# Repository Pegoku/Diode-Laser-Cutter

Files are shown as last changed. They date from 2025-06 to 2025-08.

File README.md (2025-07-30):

# Diode-Laser-Cutter

This project is a 450 nm, 10 W diode laser cutter and engraver controlled by a BTT Rodent board running the FluidNC firmware.

## Why I made it?

I made this project as I wanted to learn how to design a small laser CNC to cut and engrave plywood. I also wanted to learn how to use the FluidNC firmware, as in the future I'd like to design a desktop CNC router, and I wanted to use the same firmware and board for it.

## Features

- Laser PWM control
- 10W diode laser
- 24V PSU
- Web interface for controlling the laser

## Images

Final Build
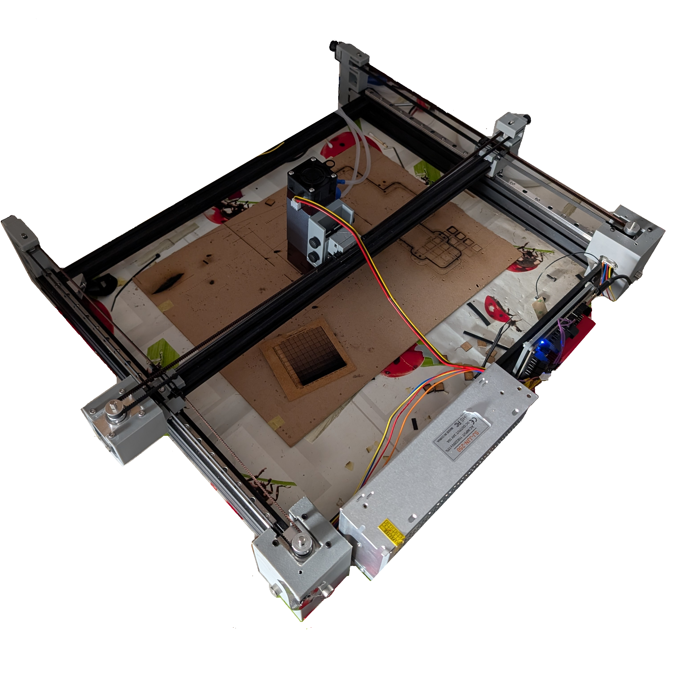
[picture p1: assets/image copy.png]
Final Build


Example of engraving
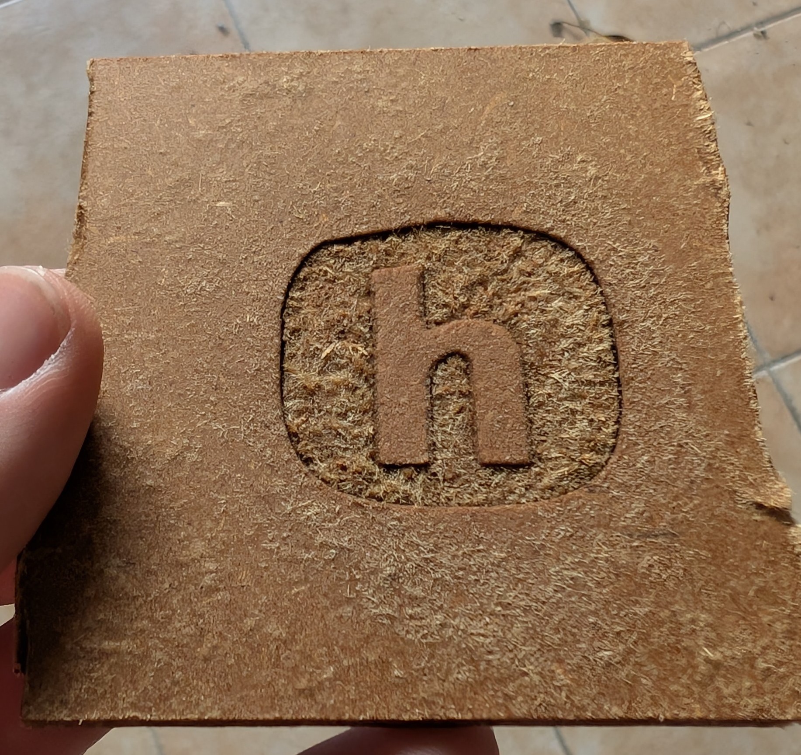
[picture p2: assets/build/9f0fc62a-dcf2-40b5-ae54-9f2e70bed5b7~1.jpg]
Example of engraving


<details>
  <summary>Final design</summary>

Final Design

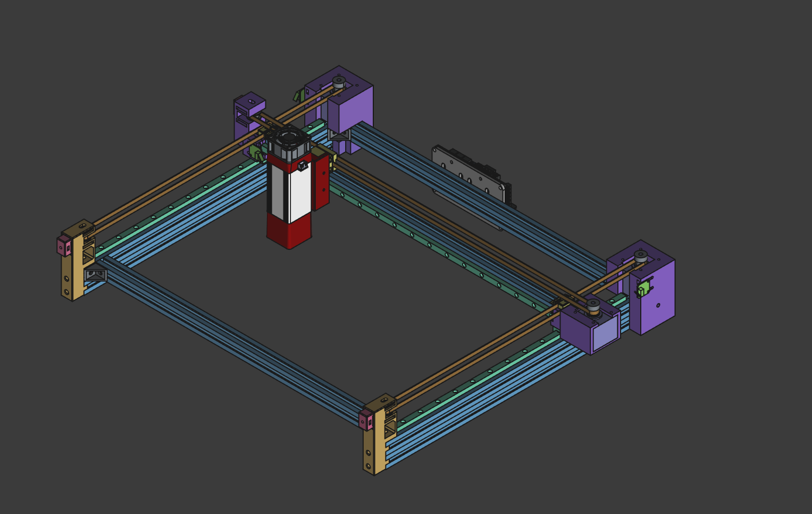
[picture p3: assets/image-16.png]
Final


</details>

<details>
  <summary>Pinout</summary>

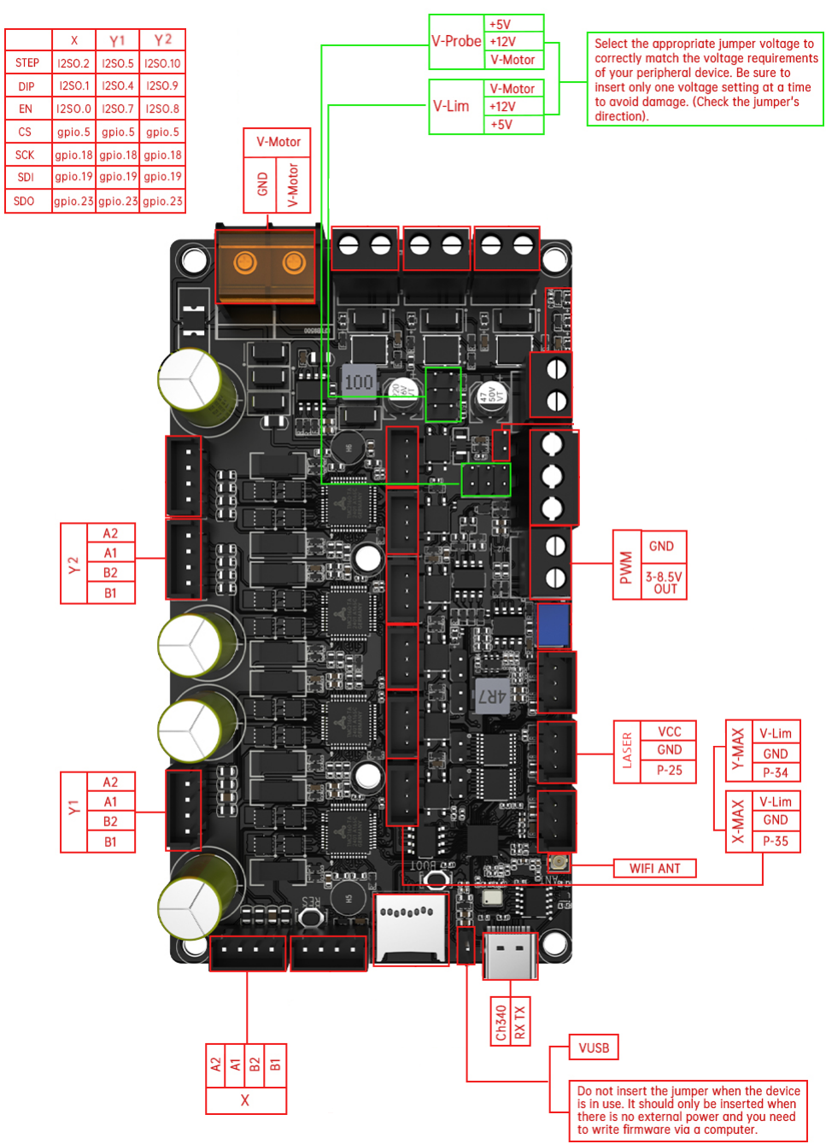
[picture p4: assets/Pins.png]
Pinout


</details>

## BOM

| Index | Part Number | What the item is for in your project | Pack Quantity | Qtty | Link | Unit Price | Total Price | Total (incl. VAT. shipping ...) | Total (incl. VAT. shipping ...) USD |
| ----- | --- | --- | --- | --- | --- | --- | --- | --- | --- |
| 1 | GT2 belt | Belt | 5m | 1 | https://www.aliexpress.com/item/1005001622058547.html | 6.09 € | 6.09 € | 300.06 € | $345.07 |
| 2 | M5x30mm pins | Belt tensioner idlers | 7 | 1 | https://www.aliexpress.com/item/1005007023343232.html | 2.25 € | 2.25 € | 4.29 € | $4.93 |
| 3 | ISO7380 M5x35mm | Screw | 10 | 1 | https://www.aliexpress.com/item/32810852732.html | 2.63 € | 2.63 € | |
| 4 | ISO7380 M5x20mm | Screw | 10 | 1 | https://www.aliexpress.com/item/32810852732.html | 1.59 € | 1.59 € | |
| 5 | ISO7380 M5x8mm | Screw | 10 | 1 | https://www.aliexpress.com/item/32810852732.html | 0.99 € | 0.99 € | |
| 6 | DIN912 M3x10mm | Screw | 50 | 1 [^*] | https://www.aliexpress.com/item/32810872544.html | 1.91 € | 0.00 € | |
| 7 | 2020 Corler bracket | Support for frame | 10 | 1 | https://www.aliexpress.com/item/1005008208638104.html | 2.44 € | 2.44 € | |
| 8 | Nema 17 stepper motor | Motor | 1 | 3 | https://www.aliexpress.com/item/1005005281739306.html | 6.59 € | 19.77 € | |
| 9 | BTT Rodent | Controller | 1 | 1 | https://www.aliexpress.com/item/1005008016124632.html | 51.34 € | 51.34 € | |
| 10 | 2020Tx500 | Aluminum extrusion | 1 | 1 | https://www.aliexpress.com/item/1005005893301224.html | 7.59 € | 7.59 € | |
| 11 | 2020Tx550 | Aluminum extrusion | 1 | 2 | https://www.aliexpress.com/item/1005005893301224.html | 8.19 € | 16.38 € | |
| 12 | T-nut M5 | T-Nut for aluminum extrusion | 50 | 1 [^*] | https://www.aliexpress.com/item/1005004157015035.html | 2.30 € | 0.00 € | |
| 13 | MGN9Cx400 | Linear Rail | 1 | 2 | https://www.aliexpress.com/item/4000264234020.html | 12.29 € | 24.58 € | |
| 14 | MGN9Cx500 | Linear Rail | 1 | 1 | https://www.aliexpress.com/item/4000264234020.html | 13.99 € | 13.99 € | |
| 15 | 2040Tx450 | Aluminum extrusion | 2 | 1 | https://www.aliexpress.com/item/1005003300082630.html | 15.69 € | 15.69 € | |
| 16 | Laser LT-80W 24V | Laser | 1 | 1 | https://www.aliexpress.com/item/1005003306807390.html | 121.94 € | 121.94 € | |
| 17 | Air pump A | Air pump option A | 1 | 1 | https://es.aliexpress.com/item/1005008823630481.html  | 6.59 € | 6.59 € | |
| 18 | Air pump B | Air Pump option B | 1 | 1 | https://es.aliexpress.com/item/1005007667077158.html  | 10.19 € | 10.19 € | |
| 19 | 24V/10A PSU | PSU | 1 | 1 | https://es.aliexpress.com/item/33051556213.html | 22.79 € | 22.79 € | |
| 20 | Limit Switches | Homing | 5 | 1 | https://es.aliexpress.com/item/1005007124540078.html  | 3.49 € | 3.49 € | |
| 21 | Discount code | Discount code | 1 | 1 | ATOLLSES40 | -40.00 € | -40.00 € | |
| 22 | Hand Screw | Belt tensioning | 10 | 1 | https://es.aliexpress.com/item/1005007775607843.html  | 2.59 € | 2.59 € | |
| 23 | Idler | Belt Idler | 1 | 3 | https://es.aliexpress.com/item/32817328238.html | 1.20 € | 3.60 € | |
| 24 | Pulley | Belt Pulley | 1 | 3 | https://es.aliexpress.com/item/32781681772.html | 1.18 € | 3.54 € | |

[^*]: Parts already owned, not included in the total price

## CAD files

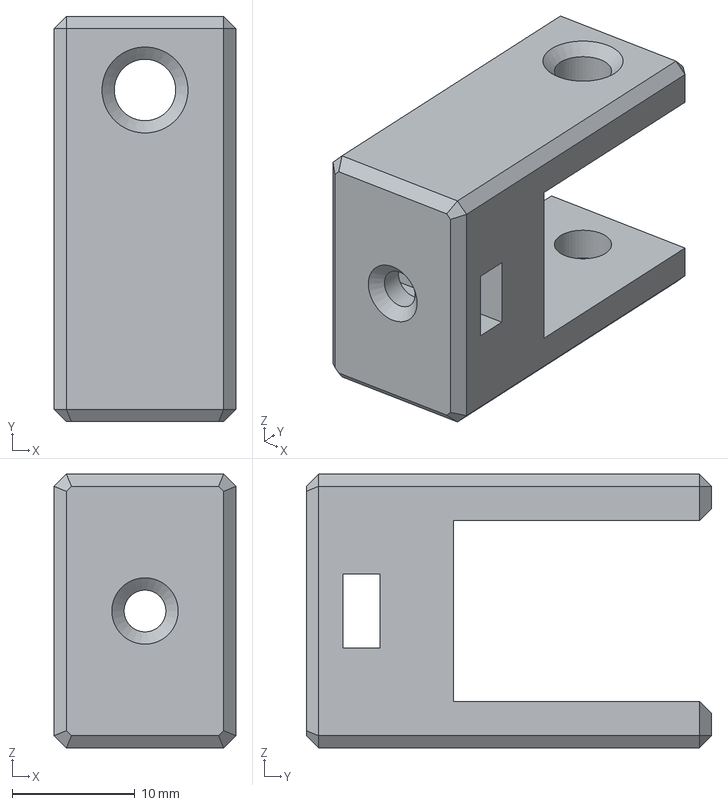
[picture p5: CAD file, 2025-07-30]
CAD/LaserCutter-X GantryBelt Tensioning3.step
14.8 x 33.0 x 22.3 mm

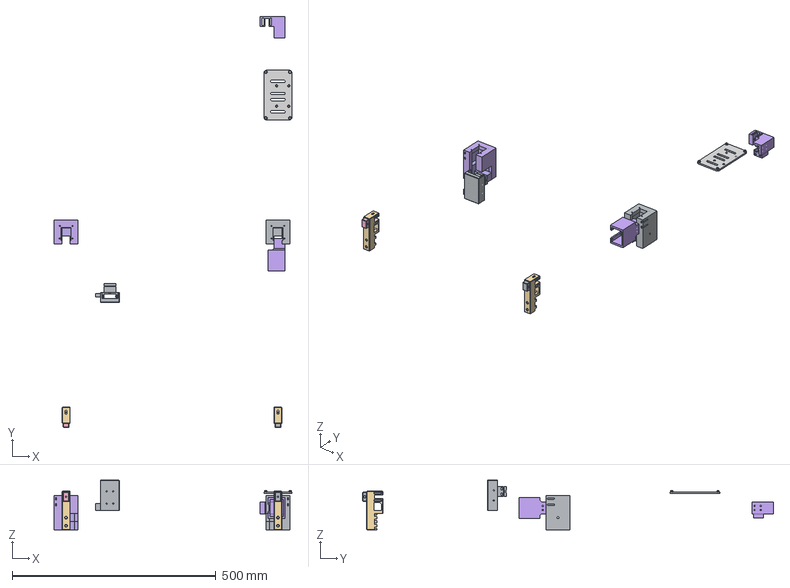
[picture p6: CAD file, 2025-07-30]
CAD/printedParts.step
583.8 x 1009.0 x 122.0 mm
Idler Support2
Belt Tensioning2
MotorHolderX2
MotorHolderX1
MotorHolderA
MotorHolderB
Belt Tensioning1
Scale002
Scale001
Idler Support

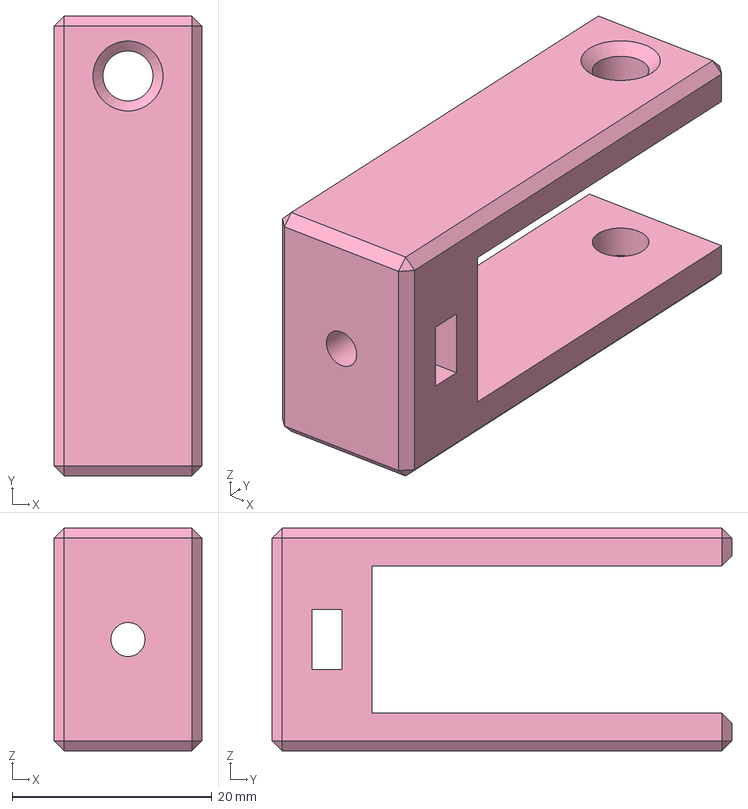
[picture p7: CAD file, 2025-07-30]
CAD/printedParts3.step
14.8 x 46.0 x 22.3 mm

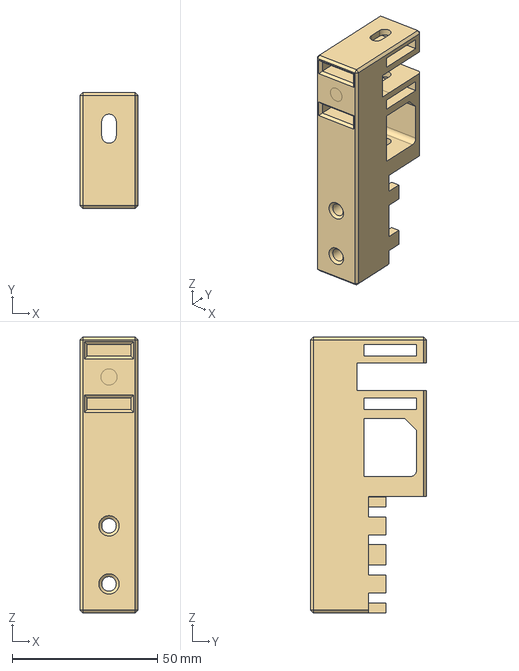
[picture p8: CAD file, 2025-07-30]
CAD/LaserCutter-Y Support 1Idler Support.step
20.0 x 40.0 x 95.0 mm

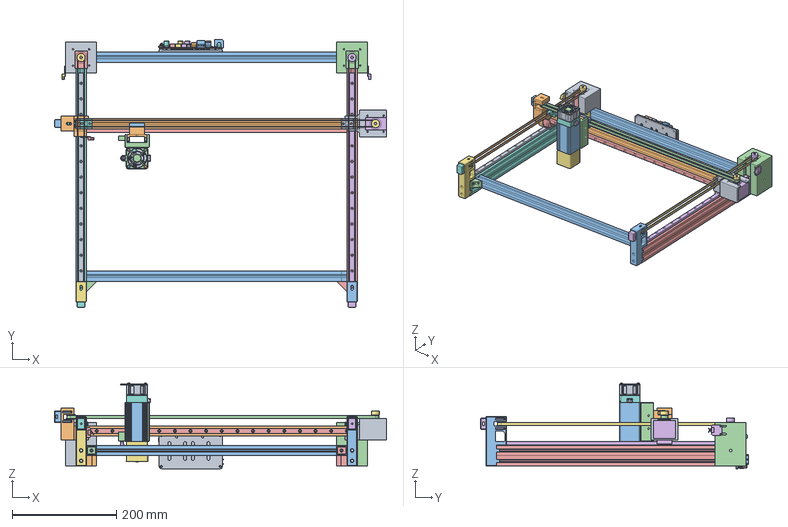
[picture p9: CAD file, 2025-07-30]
CAD/LaserCutter.FCStd
637.1 x 513.7 x 164.5 mm
DO-214AC-S1G-1.xtd
C1206 (2).xtd
C1206 (2).xtd001
C0805.xtd
C0805.xtd001
C0805.xtd002
C0805.xtd003
C0805.xtd004
C0805.xtd005
C0805.xtd006
C0805.xtd007
C0805.xtd008
C0805.xtd009
C0805.xtd010
C0805.xtd011
C0805.xtd012
C0805.xtd013
C0805.xtd014
C0805.xtd015
DFN8_3x3.xtd
DFN8_3x3.xtd001
DFN8_3x3.xtd002
DFN8_3x3.xtd003
DFN8_3x3.xtd004
DFN8_3x3.xtd005
DFN8_3x3.xtd006
DFN8_3x3.xtd007
DFN8_3x3.xtd008
DFN8_3x3.xtd009
DFN8_3x3.xtd010
DFN8_3x3.xtd011
DFN8_3x3.xtd012
DFN8_3x3.xtd013
DFN8_3x3.xtd014
DFN8_3x3.xtd015
PEC0510.xtd
PEC0510.xtd001
PEC0510.xtd002
PEC0510.xtd003
KEY-SMD_4P-L42-W32-P220-LS.xtd
KEY-SMD_4P-L42-W32-P220-LS.xtd001
KF128_3P.xtd
254_1x2PIN_DIP.xtd
XH2_54-4P_step.xtd
XH2_54-4P_step.xtd001
XH2_54-4P_step.xtd002
XH2_54-4P_step.xtd003
TSSOP-16-1.xtd
254_1x2PIN_DIP.xtd001
5.08_2Pjiexian.xtd
res_2512.xtd
XH-A-3.xtd
XH-A-3.xtd001
XH-A-3.xtd002
SL-D.xtd
3362S-1-103.xtd
5.08_2Pjiexian.xtd001
C3225-1.xtd
DO-214AC-S1G-1.xtd001
DO-214AC-S1G-1.xtd002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

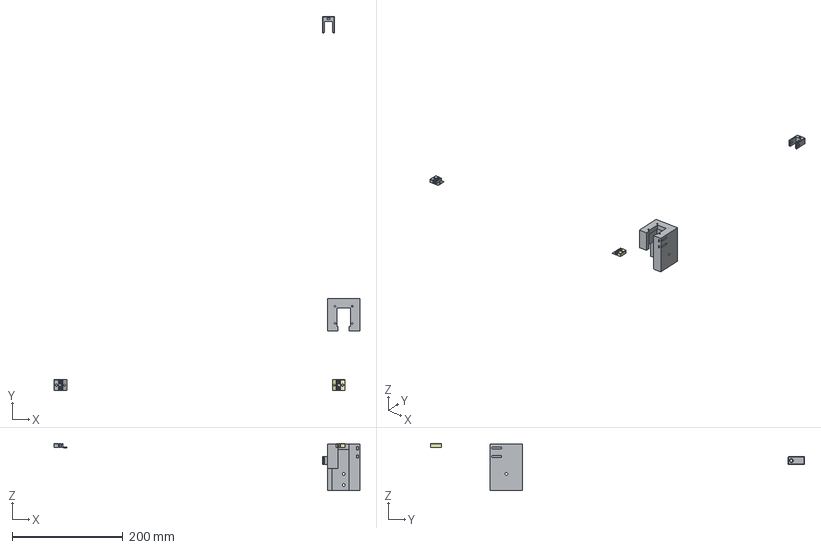
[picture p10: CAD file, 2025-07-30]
CAD/printedParts2.step
552.0 x 675.3 x 85.0 mm
MotorHolderA
Belt Tensioning3

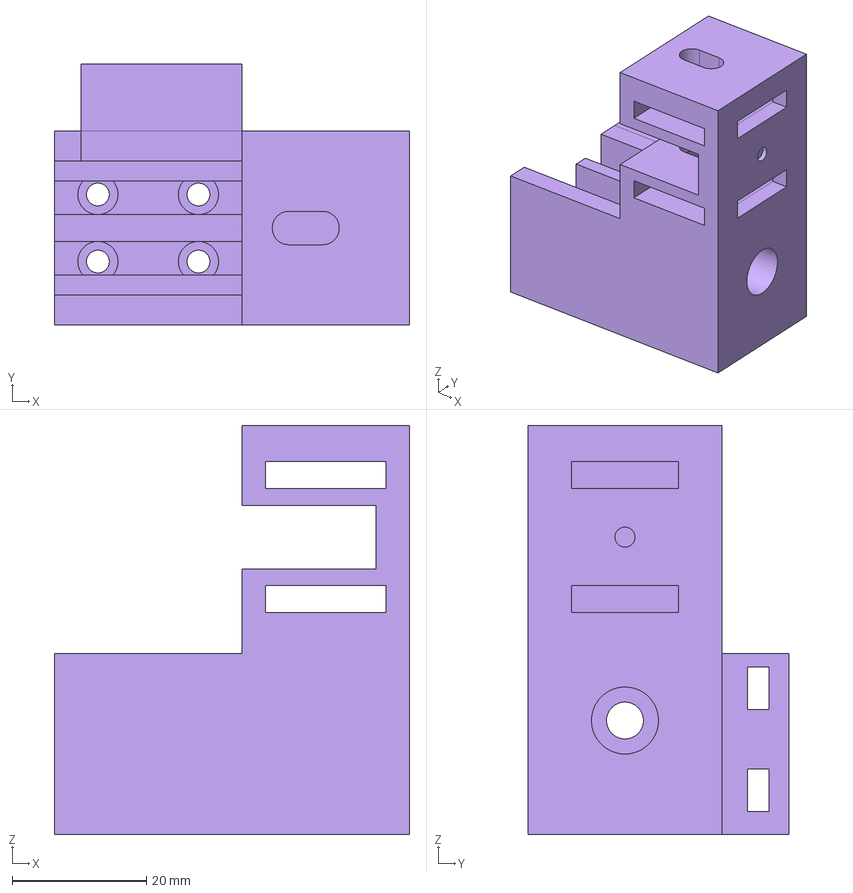
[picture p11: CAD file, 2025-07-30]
CAD/printedParts4.step
53.0 x 38.9 x 61.0 mm

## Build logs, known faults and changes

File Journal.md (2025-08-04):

|---
title: "Diode Laser Cutter"
author: "Pegoku"
description: "CNC Laser Cutter/engraver with a diode laser"
created_at: "2025-06-18"
total_time_spent: "83h"
---

# June 18th: Mockup and first components
First day of the project. I wanted to get an idea of what (and how) I'd like to build the laser cutter. That's why I did a few sketches to which I then selected the best one.
Sadly this was made during class, so I don't have any pictures of the sketches. :sob:

But I can tell you that it had a simple structure, with the dimensions of 400x500mm and a square laser head. It would use linear rails for all the axes and a ball screw on each axis to be able to move rigidly and accurately.

I would also use a CNC controller and probably one with an esp32 as I wanted to use the [FluidNC](http://wiki.fluidnc.com/en/home) firmware (a really cool firmware for esp32-based CNC controllers) as I had never used it and I love esp32.

I started looking for some components, the one of which I started with was the controller, as it would limit the components I could use. After quite a bit of research I found the [BTT Rodent](assets/https://biqu.equipment/products/bigtreetech-rodent). A full featured controller, It is a bit overkill for my project, but I wanted to try it out, as in the future I would like to do a CNC router and could use it for that too, so I'd already be experienced with it.

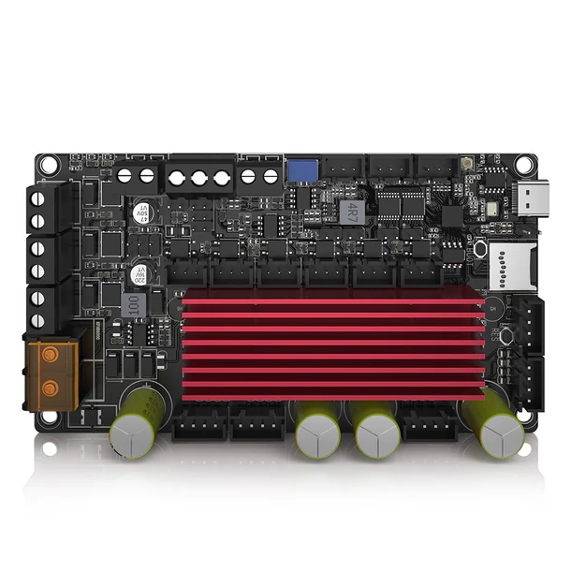
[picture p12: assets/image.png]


Once I arrived home, as I already had the controller, I searched for a laser, and after quite a bit of searching, I went with a Diode Laser, as it was the most affordable option and it could cut wood and acrylic, which is what I wanted to cut. I found this [laser](https://es.aliexpress.com/item/1005003306807390.html) on aliexpres, it was quite pricey (for the budget I have), but it's the best one I could find with that specs. It has a 10W output, which is enough to cut 5mm wood and acrylic, and it has a square head, which will be helpful for the mounting bracket.

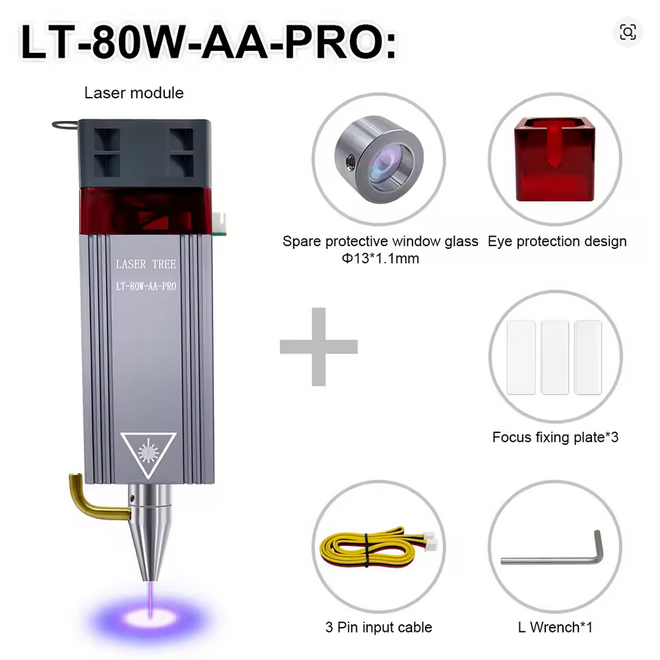
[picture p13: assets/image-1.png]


After that, I started looking for the structure I wanted to do. I planned in the sketches I'd use 2020 aluminum extrusions, so I started looking for them. I first checked aliexpress, but they were quite expensive, so I searched for other suppliers, and found JLCMC, a subsidiary of JLCPCB, which is a PCB manufacturer. They had a really good price for the extrusions, so I started using them for the structural materials. 
I ended up with:
- 1x 2020x540mm extrusion, as I wanted to have 20mm of space on each side - X axis.
- 2x 2040x440mm extrusions, as I wanted to have 20mm of space on each side too, and 2040 would help the the machine be more rigid and taller. - 2x Y axis.

Then, I started looking for the linear rails, and did quite a bit of research, but it was getting late, so I decided to leave it for the next day.

PS: sorry for not having images of the sketches

**Total time spent: 8h**

# June 19th: More components and starting the design
Today was the first day of summer holidays, so I had all day to work on the project.
First, I continued looking for the linear rails. I didn't know which ones to choose, as I have never used them before, so I had to do research (the best part of all projects). As I was looking for them in JLCMC, there were quite a few options, but I ended up with the BMW9C-1-L500-Z1-C-E20 linear rails. They weren't too expensive, and had the characteristics I wanted, so I went with them. I got 1x 500mm rail for the X axis, and 2x 400mm rails for the Y axis.

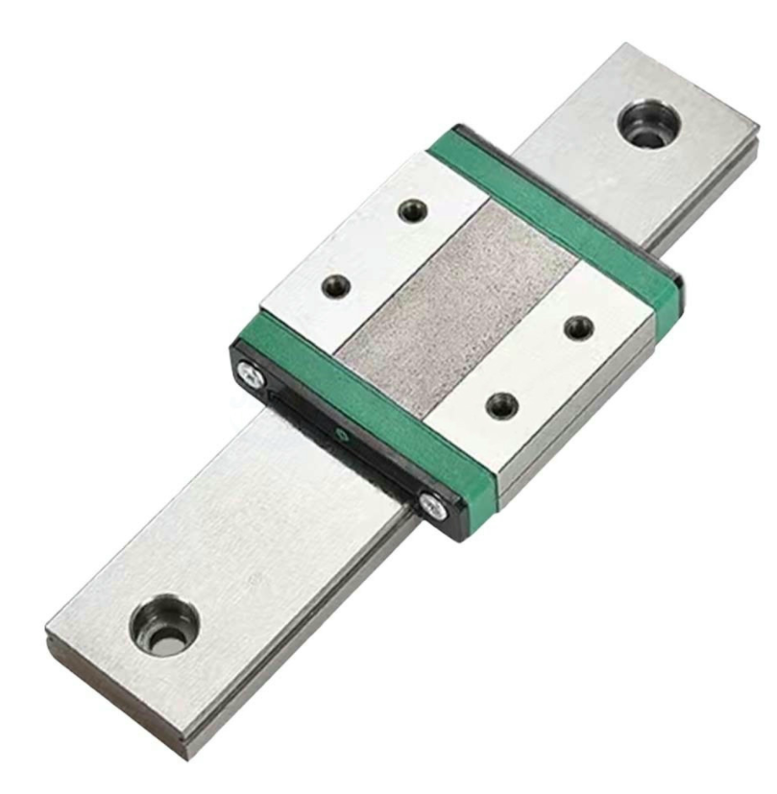
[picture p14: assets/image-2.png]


And now the last component I needed (for the base structure) was the ball screws. I thought they would be cheap (that's why I wanted to use them), but they were quite more expensive than I expected. So I thought for quite long, other ways I could use to move the axes, and ended up using GT2 belts. They are not as rigid as the ball screws, but they are way cheaper and easier to find.

After having the basic parts, I started designing the base of the frame in FreeCAD.
I started creating a template for the 2020 extrusions so I could easily create new ones of any size.

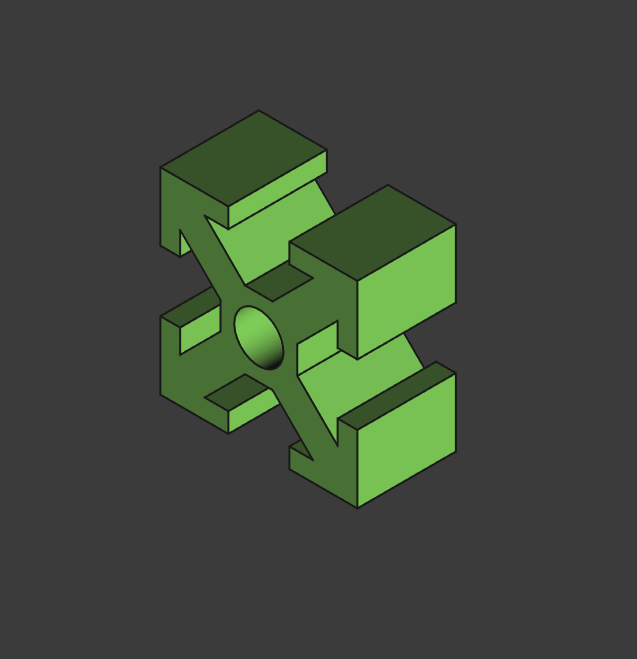
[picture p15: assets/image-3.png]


I did the same for the linear rails. I also searched for a 3d model of the Rodent controller, which was quite hard, but I finally found it.

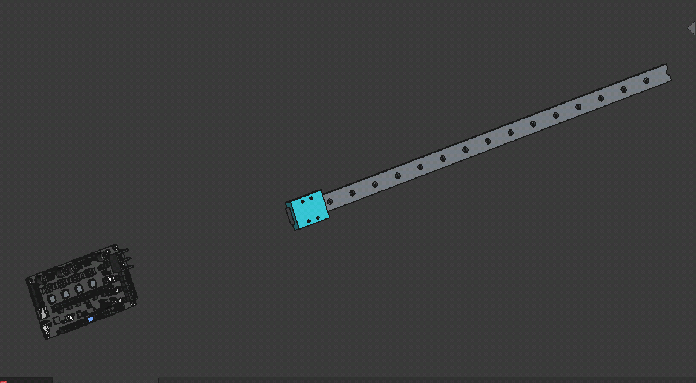
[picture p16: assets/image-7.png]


After that, I started creating the base frame. First, I did the X axis, which was quite easy, as it was just a 2020 extrusion with a linear rail.

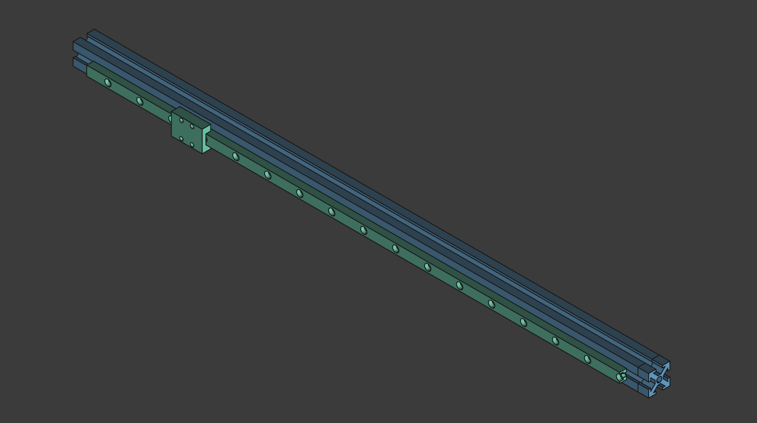
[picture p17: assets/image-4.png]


Then I did the Y axis. I had to do 2x as I wanted to have 2 Y axes, one on each side of the X axis. I used 2040 extrusions for the Y axis, as I wanted it to be more rigid and taller. I also added the linear rails to the Y axis.

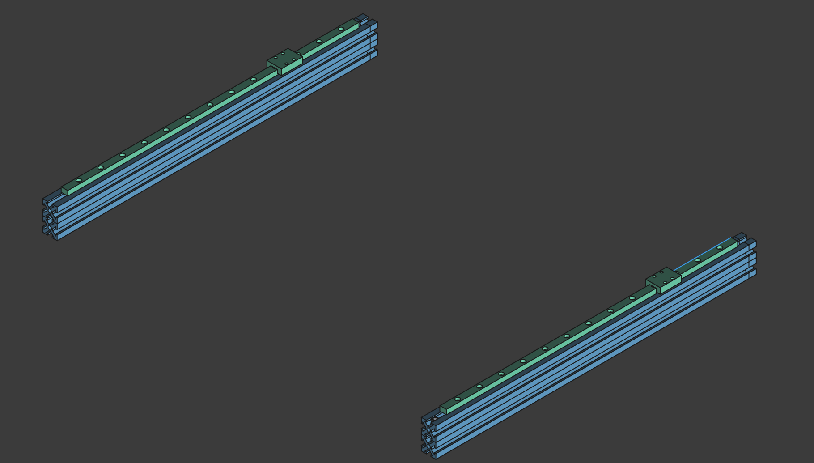
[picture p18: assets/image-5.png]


After that, I combined everything to create the base frame. I also added a rear 2020 extrusion to hold the Y axes together.

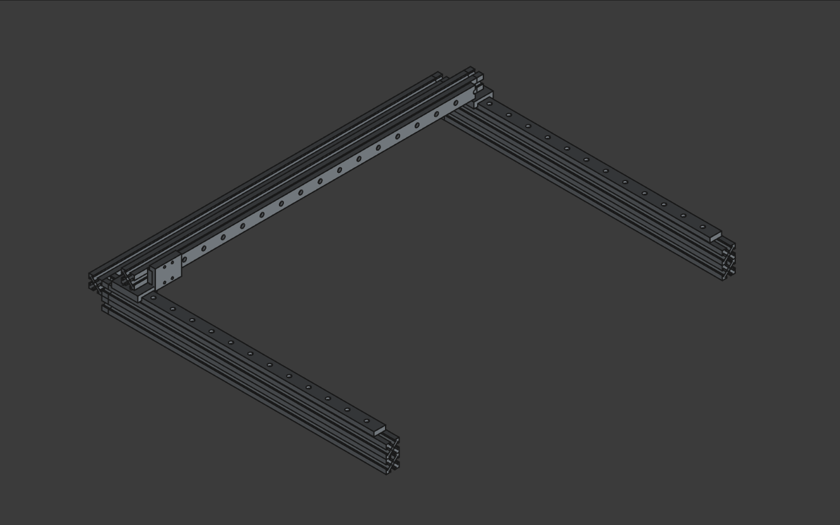
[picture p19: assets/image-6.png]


## Motors and pulleys
Now I had to find the motors I would use. I didn't know which ones to use, nor how many or where to put them, so I did some research and found that NEMA 17 motors would be the best option for this lightweight machine. What I wan't sure was about the Y motor, I wanted to use 2x motors, one on each side of the Y axis, but it seemed a bit too much, also the controller only has 1 Y stepper output. But when I realised how easier it would be to have 2x motors, I decided to use one of the remaining stepper drivers (Z) for the second motor.

Then, I searched how would the belts be mounted, but ended up leaving it for the future me, as I didn't know how to do it currently. What I did was to add the [motors](https://es.aliexpress.com/item/1005005281739306.html), [pulleys](https://es.aliexpress.com/item/32781681772.html) and [idlers](https://es.aliexpress.com/item/32817328238.html) to the model. 

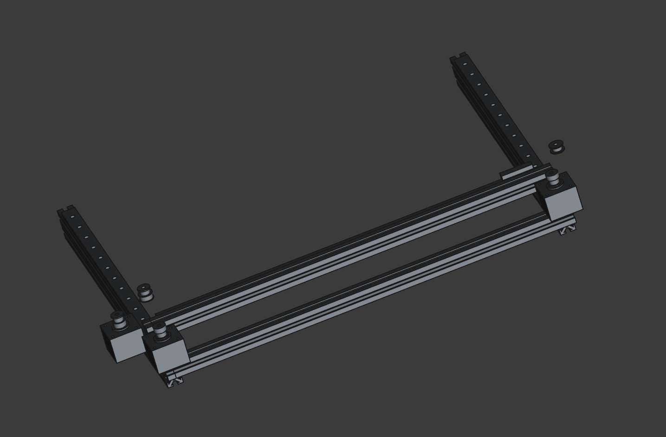
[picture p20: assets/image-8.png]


Now was time for one of the hardest parts of the project (imo, for now). The belt tensioners. I have never used nor designed them, so I had to search online what they are, how they work and maybe some example. Luckily I found a tutorial on how to tension GT2 belts on a voron 2.4, which helped me to understand how they work and how I could design one. I ended up with a a quite simple design, which I think will work. It consists of a 3d printed support for the idler, with a C-shaped piece and a 30mm M5 pin for the idler to be mounted on. The C-shaped piece has a hole with a M3 nut where a M3 screw will be used to tension the belt. I'm not sure if it will work, nor if I explained it well, but I will show you the model so you can see how it works.

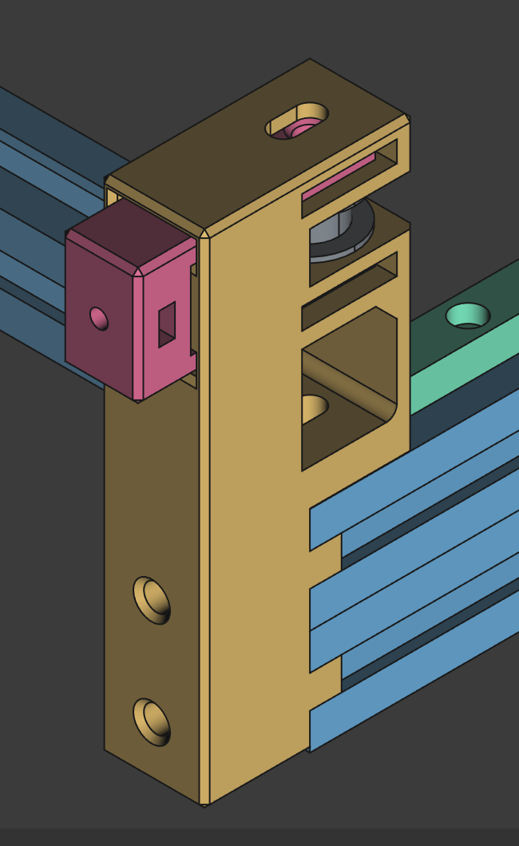
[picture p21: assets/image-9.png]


To continue, I had to find a way to mount the motors to the frame. I started with the Y motors as they seemed the easiest ones. I designed a simple bracket that would hold the motor to the 2020 extrusion. I'm not sure if it's the best way to do it, but it seems to work.

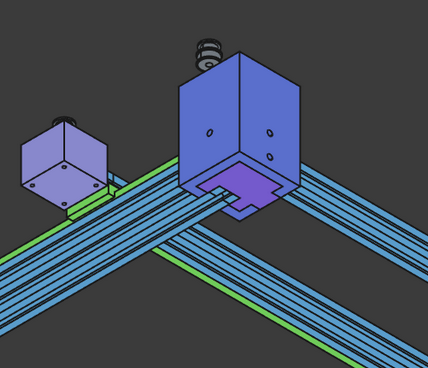
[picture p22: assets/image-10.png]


**Total time spent: 13h**

# June 20th: Continuing with the design and JLC SHIPPING!

## JLC shipping!
While designing, I checked the JLC shipping price. But what happened was unexpected, the shipping price was over 120$! This was a no-go, as I didn't have that much budget for the project, so I had to search for other supplier and ended up with the original aliexpress ones. They were a bit more expensive, specially the aluminum extrusions, but the shipping was free (and faster), so it was a way better option. The aluminum extrusions were the same, but the linear rails were a diferent model, they were MGN9C instead of BMW9C. Hope they work.

## Motors and Belts
Now I had all the tensioning components for the belts for Y axis. This is how it looks like:

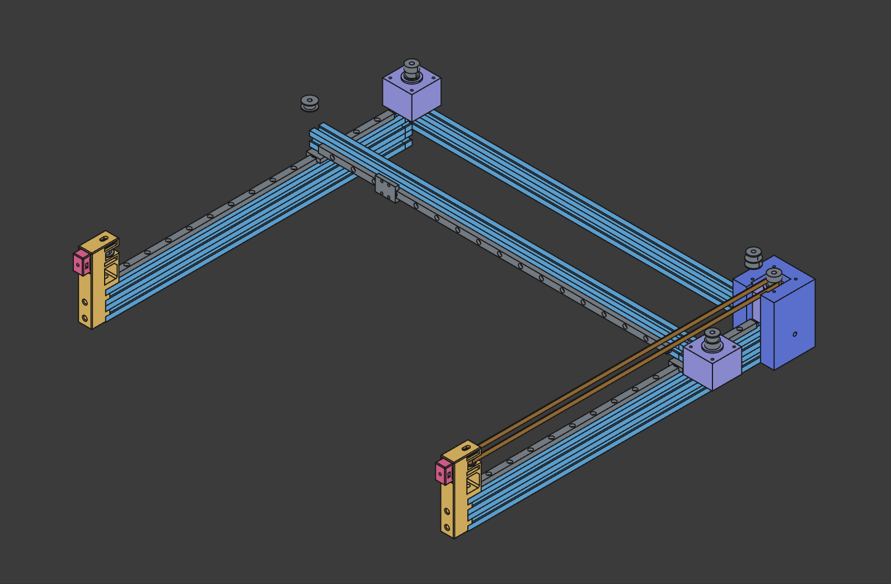
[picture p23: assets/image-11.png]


I also designed the X axis motor mount, which worked as the mount for the rail too.

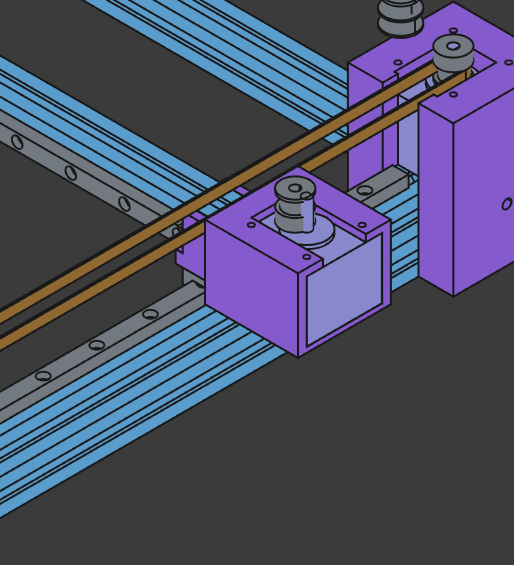
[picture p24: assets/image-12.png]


Once I had the motor mount, I started designing the X axis belt tensioner. It was quite similar to the Y axis one, but the main piece had a diferent shape, as it had to be mounted on the 2020 extrusion and it had to be used as a support for the linear rail.

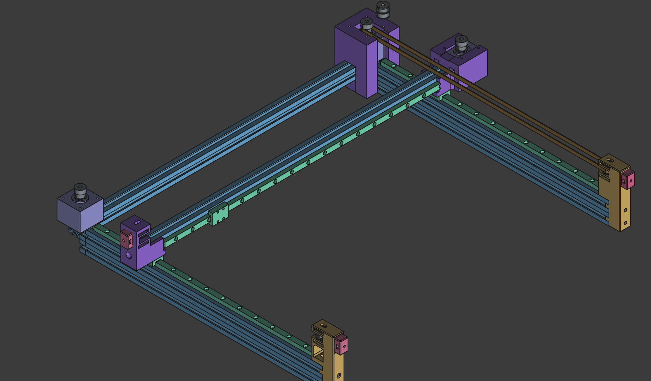
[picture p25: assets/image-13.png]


After that, I added the 2nd motor holder which was the same as the first one, but mirrored. I also added a 2020 extrusion to the front of the frame to hold the Y axis together. And to secure it I added 2020 brackets to the extrusions.
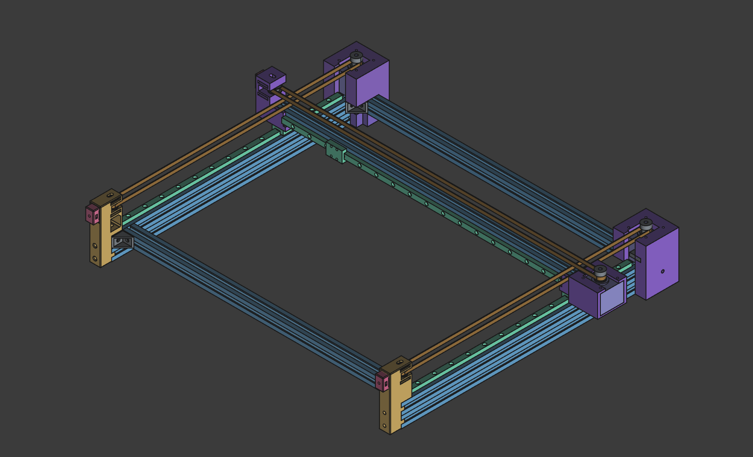
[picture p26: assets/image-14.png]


**Total time spent: 9h**

# June 21th: Aliexpress shopping
Today I didn't want to design much, so I just focused on searching for the components and trying to get the best deals I could find.

I spend all day searching for the components, and ended up with quite a good list. It was overbudget, but luckily, I got a 40€ discount coupon, so I could buy everything I needed, and still have some budget left. Sadly the coupon ends in 4 days, so I hope i get accepted before that.

[BOM](BOM.csv)

**Total time spent: 8h**

# June 22th: Laser head and coding
Today was the last day. I had to design the laser head, which was the last part of the machine.
I used the original laser head, and created a mount for it. Luckily, I found a 3d model of the laser head, so I just had to create a mount for it. I designed it to be mounted on the X axis rail, and to be able to move up and down, so I could focus the laser.

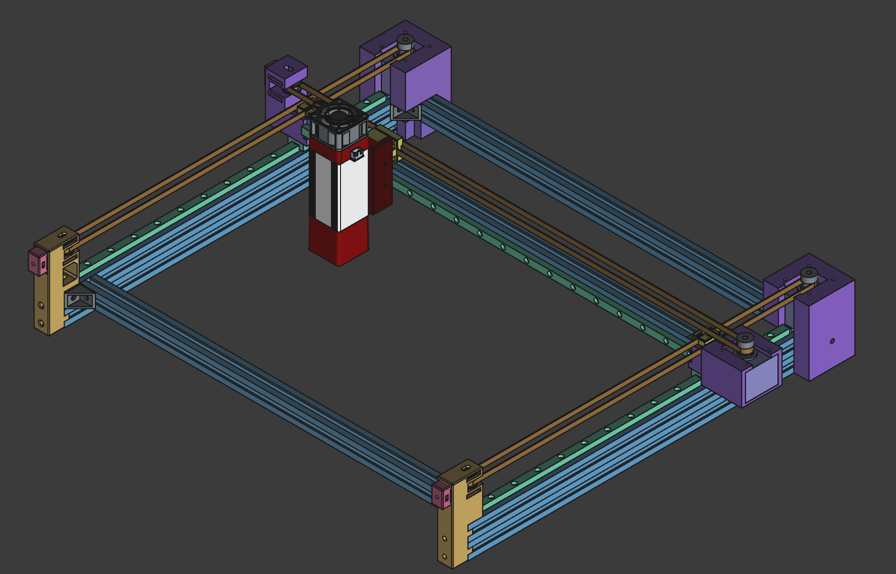
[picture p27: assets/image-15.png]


As a last thing, I added endstops to the machine, and the controller mount. The endstops were quite easy, once I found a good endstop, and the controller was quite easy too.

Final design:



Now I only had to code the machine. I used FluidNC, and luckily, there was a template for the Rodent controller, so I just had to copy it and change a bit the configuration. eg. adding dual Y motors, enabling PWM, etc.

**Total time spent: 7h**

# July 22th: Start the build
After quite a long wait. All (almost) the pieces have arived!!
Today I started the build. First, I built the frame to see how big it would be, and to see if I had the minimum pieces to build it. I did it, but the floor was a bit uneven, so I put some wood under the legs to make it flatter. 
Then I realized I had to cut the 2020 extrusions, as they were too long, so I cut them to about the right size using a hacksaw.

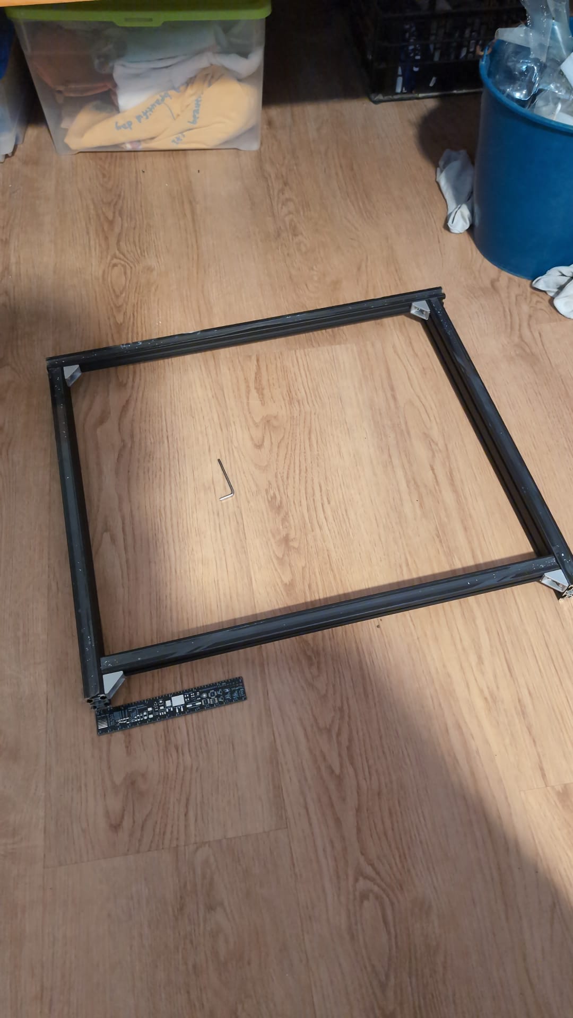
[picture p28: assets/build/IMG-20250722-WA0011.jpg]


After that, I grabbed all the printed parts I had, and started removing the supports. That took quite a while, as I had used auto-generated supports, which were quite hard to remove. But I finally got them all removed.

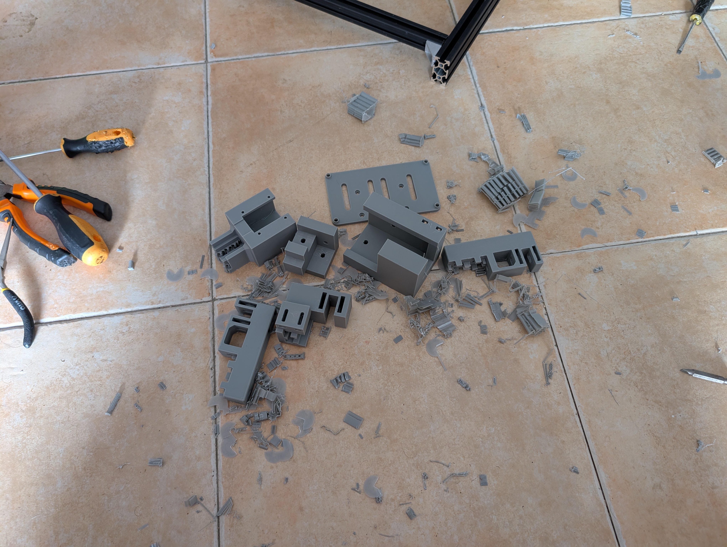
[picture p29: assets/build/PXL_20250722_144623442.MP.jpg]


To continue, I placed the motor in the printed case, and I had to modify it a bit, as I hadn't thought about the motor connector, so I had to cut a bit of the case to make it fit. After that, I placed the motor in the case and it fit snugly.

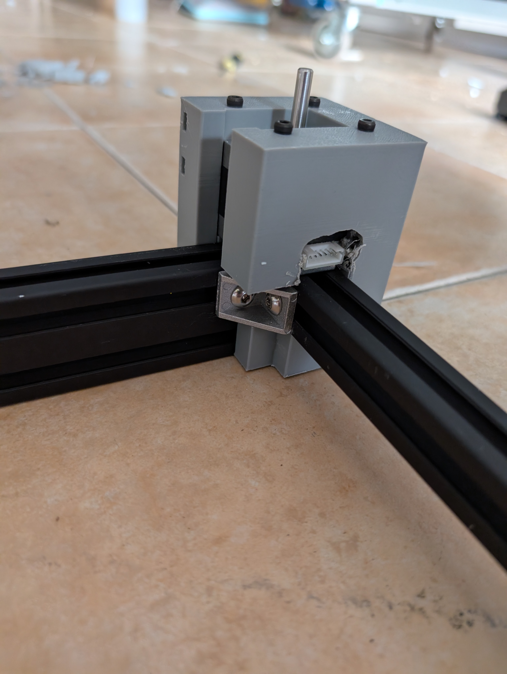
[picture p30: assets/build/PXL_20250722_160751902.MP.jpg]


Then I placed both Y idler supports, which fit snugly too. 

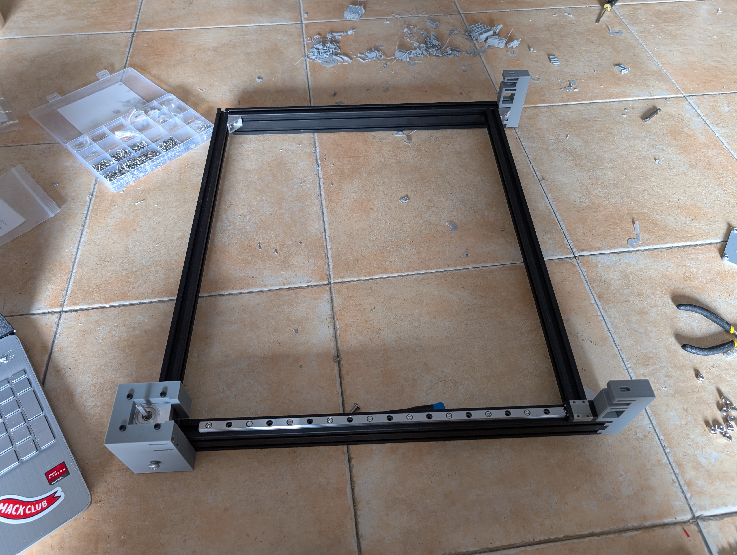
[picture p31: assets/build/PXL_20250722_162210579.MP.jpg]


After that, I screwed both Y linear rails to the extrusions. I also added the idlers to the supports, which they weren't correctly designed, as the idlers couldn't be tensioned.

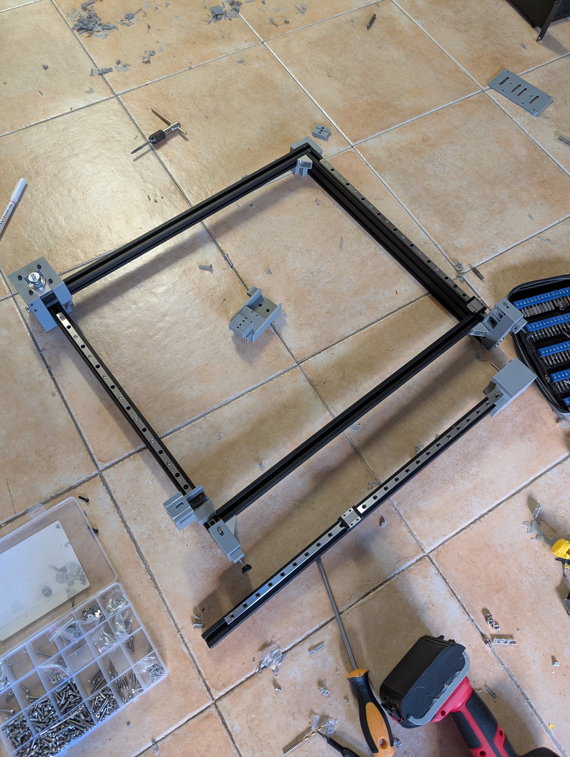
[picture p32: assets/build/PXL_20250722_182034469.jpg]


To fix: motor holders and idler supports.

**Total time spent: 6h**

# July 23th: Continuing the build
Today I continued the build. All the fixed and remaining prints finished printing.
First, I placed the 2nd motor, which I already had printed, so I had to modify it too.

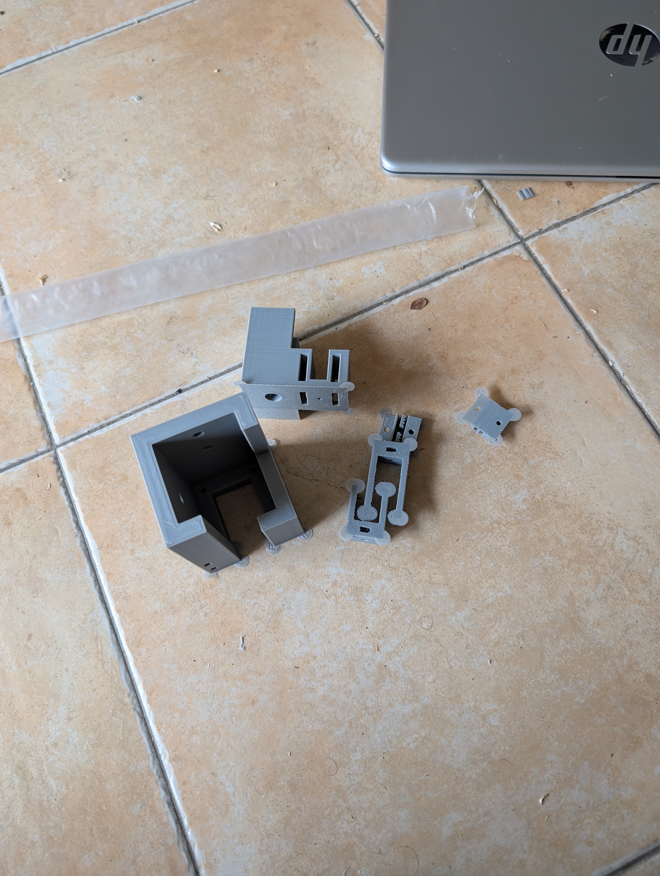
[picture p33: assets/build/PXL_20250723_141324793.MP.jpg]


Then, I screwed the X linear rail to the X axis extrusion, and aligned it with the printed pieces. 

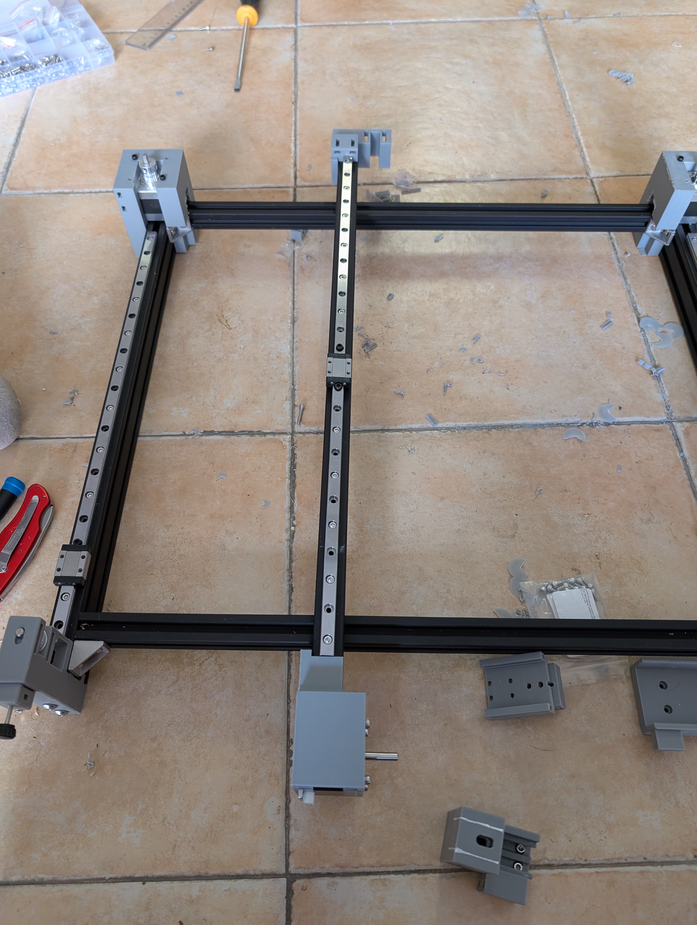
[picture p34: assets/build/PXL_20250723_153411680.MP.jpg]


Afterwards, I realised that the X axis would be hard to place, as the extrusion was on top of the screw holes. So I had to remove the printed parts from the X extrusion, remove the linear blocks from the rails and screw them to the printed parts. I used a holder-thingy to hold the balls from the linear blocks, so they wouldn't fall out. Then I slowly placed the linear blocks on the rails. This was a tense moment, as I didn't want to lose any balls, but luckily it worked and I could mount the X axis!

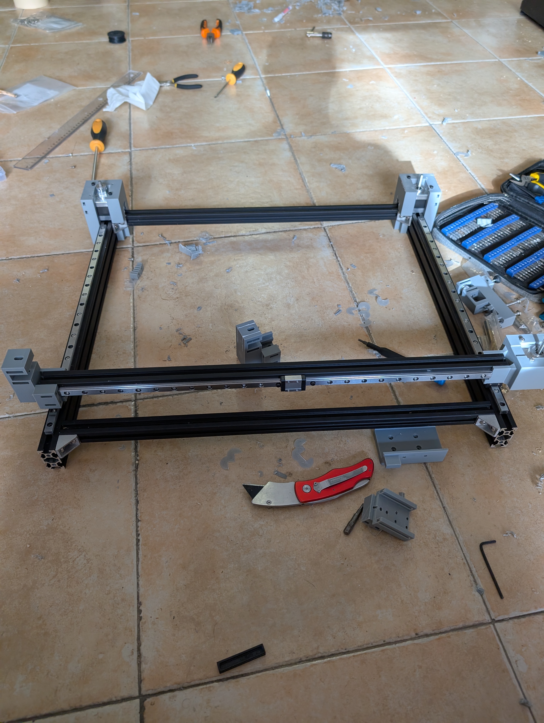
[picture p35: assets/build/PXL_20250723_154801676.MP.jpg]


To finish, I placed the new idler supports, which were designed to be able to fit the idlers and to be tensioned. I also placed the new X idler mount, which also had a design error.

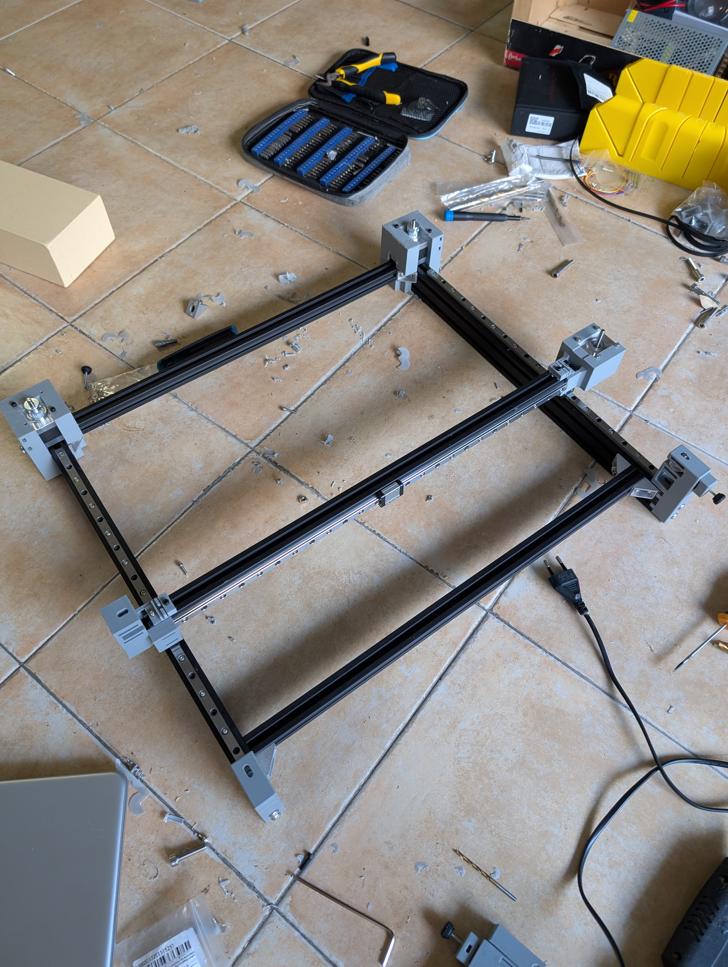
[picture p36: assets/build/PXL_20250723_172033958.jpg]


PS: I also noticed the screws I needed to use M6 screws for the extrusions, not M5, so I went and bought some M6 screws, as I didn't have any, and the next day I'll screw them to the extrusions.

**Total time spent: 5h**

# July 24th: Tapping is my passion 😭
First, I fixed the belt tensioners, as the nut was too loose and it spun freely, as I didn't use a square nut, so I just used hot glue to hold it in place. I also added a M2.5 washer to the M3 screw end, so it wouldn't damage the plastic when tightening it (it did before). 

Today I spent a LOT of time tapping the extrusions (I spent +3.5h tapping), but it was worth it. I had to tap all the extrusions, and drill some passthrough holes for some screws. I used a M6 tap, and also had to drill the printed parts to fit the M6 screws.

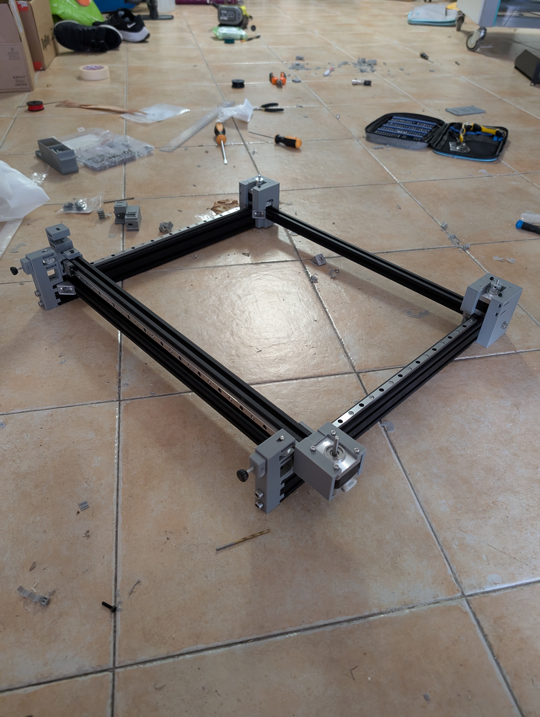
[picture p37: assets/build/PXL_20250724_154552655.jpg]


I made another mistake, one of the rear motor screw wasn't long enough, so I had to spin fast the screw so it melted the plastic and could screw to the extrusion. 

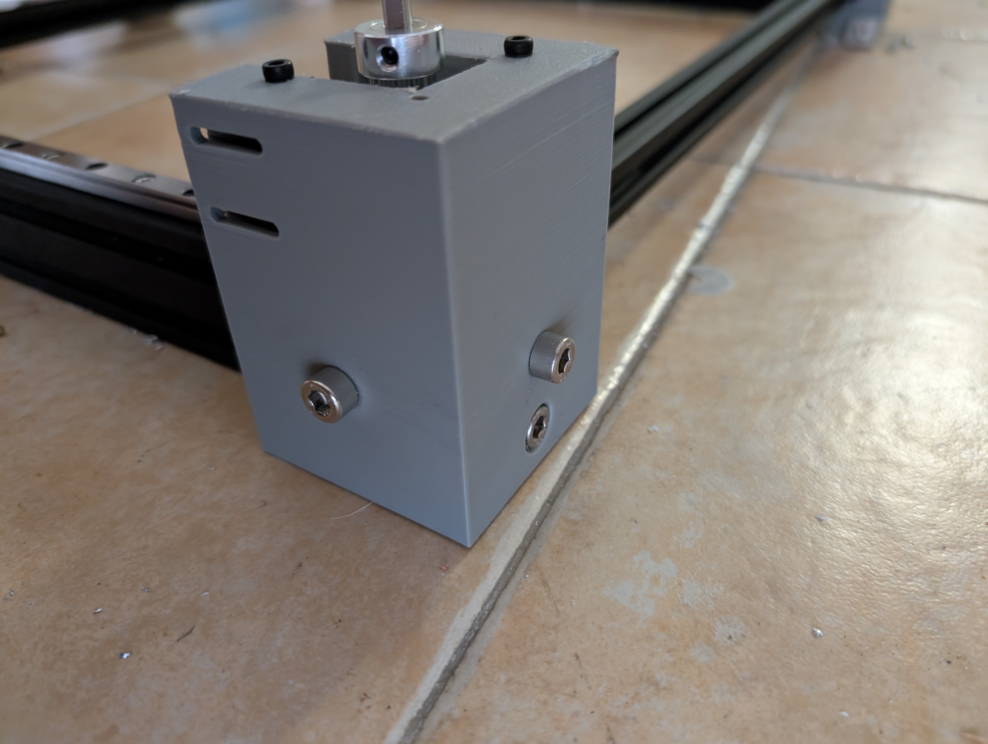
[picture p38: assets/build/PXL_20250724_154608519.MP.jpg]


But overall, I think it turned out quite well.

I also mounted the Laser on the X axis, which was quite easy, except for the fact that I had to drill new holes to the laser support, as I had designed it wrong. Was an easy fix, though.

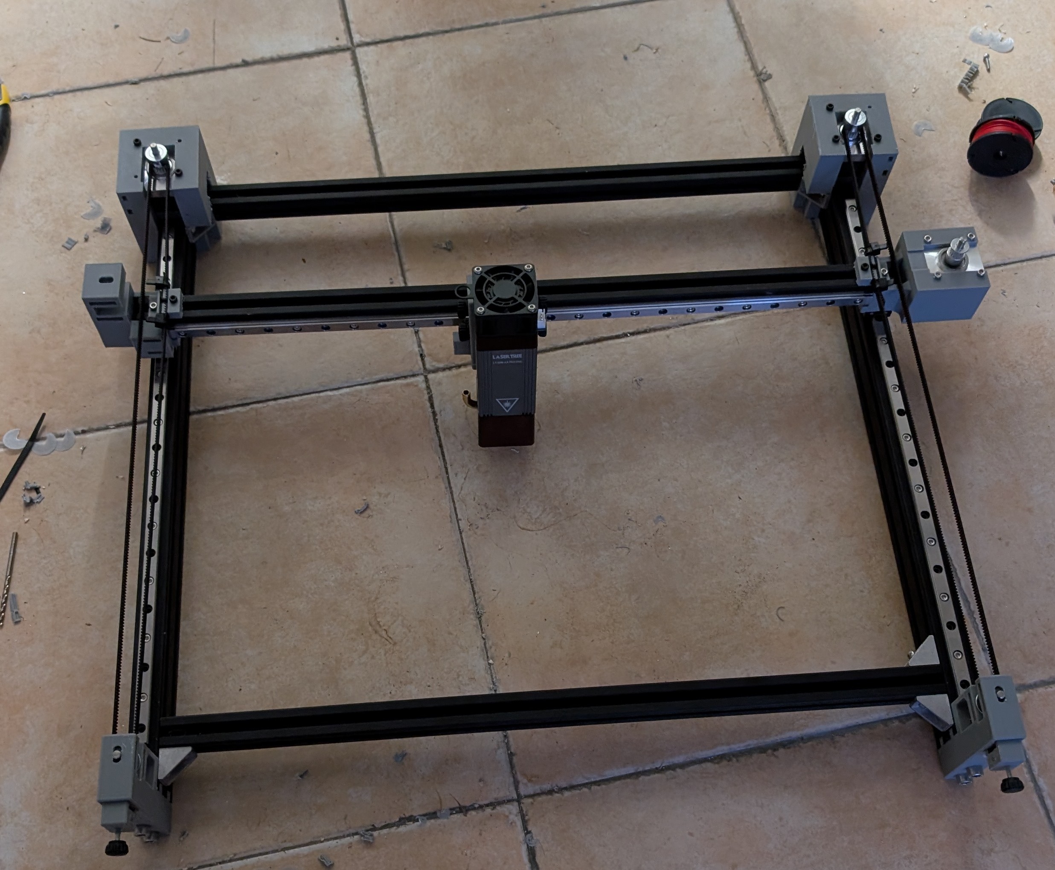
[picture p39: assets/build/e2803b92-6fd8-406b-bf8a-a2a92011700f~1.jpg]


Also, while I was at it, I wanted to connect the laser belt, but I realised I had only ordered 2 pulleys and idlers for the printer, and I needed another one, so I ordered them online, and to skip the wait, I tried getting them from an old printer I had, but sadly they were too small, so I just had to wait for them to arrive.

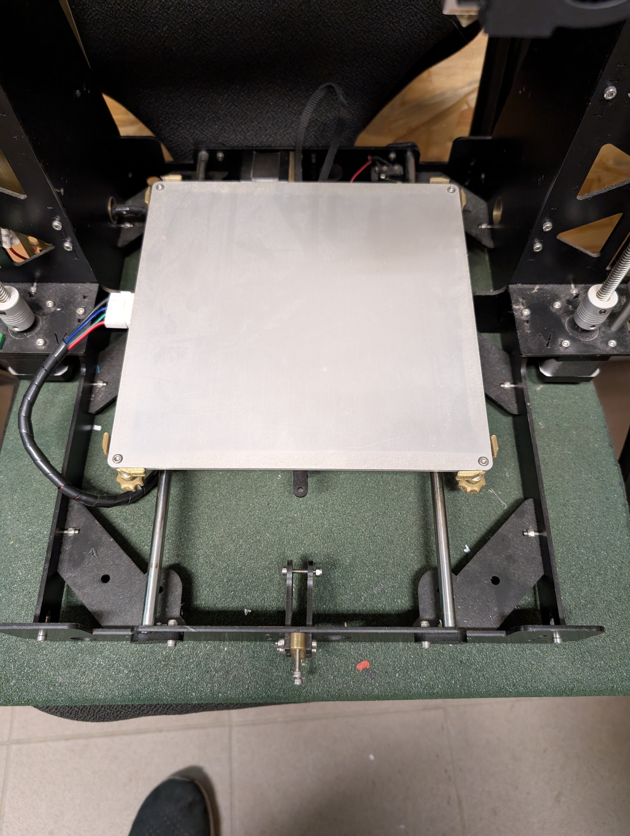
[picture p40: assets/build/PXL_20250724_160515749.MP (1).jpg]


**Total time spent: 7h**

# July 25th: Electronics and wiring
Today I mounted the electronics to the frame, and started wiring everything.
First, I mounted the controller (BTT Rodent) to the frame, which was quite easy, as I just had to screw it to the frame using T-nuts. I also mounted the power supply, which was a bit harder, as I wanted it to be mounted using t-nuts too, but there weren't any holes. So I just dissasembled the PSU and replaced drilled two nuts of the PSU and replaced the screws with longer ones so I could screw it to the frame.

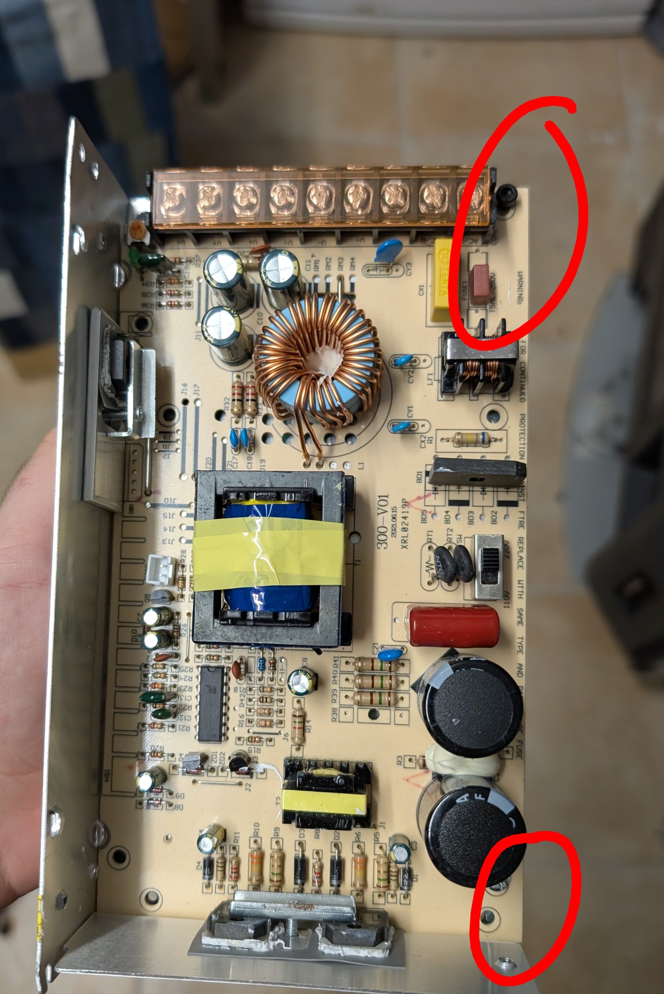
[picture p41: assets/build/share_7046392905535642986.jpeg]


I also wired the controller and power supply, I only needed to wire the laser, and motors.



**Total time spent: 5.5h**

# July 26th: Wiring the Y motors
Today I wired and configured both Y motors, which was quite easy. Sadly, I didn't have a crimper in hand, nor the right connector, so I just used pin receptacles soldered to the stepper wires. First, I thought I had configured something wrong, (maybe too little current), so I increased the current to 3A, twice the motor current, but it still didn't work, it just vibrated. Then I noticed I had connected a motor phase in reverse, so I just swapped the wires, and it worked! Then I played with them a bit, and also used the laser for the first time, which was quite fun. While doing that, I realised the motors were quite hot, and I didn't remember why. But while reviewing the config, I saw the 3A current 😅 , so I reduced it to the recommended 1.5A, and it worked perfectly.

<video controls src="assets/build/PXL_20250726_225948615~2.mp4" title="Title"></video>

**Total time spent: 3h**

# July 27th: Wiring the X motor and belt
Today the pulleys and idlers arrived! So I could wire the X motor and belt. I first mounted the idler, which was quite easy, except for a design flaw, which made the belt tensioner almost unusable. Then I mounted the pulley to the motor, which was quite easier, as I just had to use a M3 setscrew to hold it in place.
Then, I mounted the belt to the X axis, which was a quite hard to tension, but luckily I was able to do it using zipties.

After that, I crimped the wires to the motors, wired and configured them.
Then, I did some calibrations to the laser, like, the power and speed, speed and passes, accuracy, and my favourite, the shake test.









Shake test

While doing the tests, I fixed the config, and finally I did my first real ~~print~~ cut. It was for my robotics team, and it was a success!!, quite fast too. I did with cardboard, and then with wood.



**Total time spent: 7h**

# July 28th: Final configuration and 3d engraving!
Today I finished the configuration of the laser, and also wanted to test something I saw online. 3D engraving. To do it, I tested with the HackClub logo, which I had to convert to a grayscale image, and then to gcode using LaserGRBL. The result, after quite a few tries, was quite good.

First try:



Second try:



Second try after cleaning:



**Total time spent: 4.5h**

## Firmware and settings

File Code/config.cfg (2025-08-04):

board: BTT Rodent V1.0
name: BTT CNC
meta: (07.2025) by Pegoku
kinematics: {}
stepping:
  engine: I2S_STREAM
  idle_ms: 255
  pulse_us: 4
  dir_delay_us: 1
  disable_delay_us: 0
axes:
  shared_stepper_disable_pin: NO_PIN
  x:
    steps_per_mm: 40
    max_rate_mm_per_min: 10000
    acceleration_mm_per_sec2: 1000
    max_travel_mm: 300
    soft_limits: false
    homing:
      cycle: 1
      positive_direction: false
      mpos_mm: 150
      feed_mm_per_min: 200
      seek_mm_per_min: 200
      settle_ms: 500
      seek_scaler: 1.1
      feed_scaler: 1.1
    motor0:
      limit_neg_pin: NO_PIN
      limit_pos_pin: NO_PIN
      limit_all_pin: gpio.35:low
      hard_limits: false
      pulloff_mm: 1
      tmc_5160:
        step_pin: i2so.2
        direction_pin: i2so.1
        disable_pin: I2SO.0
        cs_pin: gpio.5
        spi_index: 1
        r_sense_ohms: 0.022
        run_amps: 1.5
        hold_amps: 0.5
        microsteps: 8
        toff_disable: 0
        toff_stealthchop: 5
        use_enable: false
        run_mode: CoolStep
        homing_mode: Stallguard
        stallguard: 3
        stallguard_debug: true
        toff_coolstep: 3
        tpfd: 4
  y:
    steps_per_mm: 40
    max_rate_mm_per_min: 10000
    acceleration_mm_per_sec2: 1000
    max_travel_mm: 300
    soft_limits: false
    homing:
      cycle: 1
      positive_direction: true
      mpos_mm: 150
      feed_mm_per_min: 100
      seek_mm_per_min: 200
      settle_ms: 500
      seek_scaler: 1.1
      feed_scaler: 1.1
    motor0:
      limit_neg_pin: NO_PIN
      limit_pos_pin: gpio.34
      limit_all_pin: NO_PIN
      hard_limits: false
      pulloff_mm: 1
      tmc_5160:
        step_pin: i2so.5
        direction_pin: i2so.4:low
        disable_pin: I2SO.7
        cs_pin: NO_PIN
        spi_index: 2
        r_sense_ohms: 0.075
        run_amps: 1.5
        hold_amps: 0.5
        microsteps: 8
        toff_disable: 0
        toff_stealthchop: 5
        use_enable: false
        run_mode: CoolStep
        homing_mode: CoolStep
        stallguard: 3
        stallguard_debug: false
        toff_coolstep: 3
        tpfd: 4
    motor1:
      limit_neg_pin: NO_PIN
      limit_pos_pin: gpio.33
      limit_all_pin: NO_PIN
      hard_limits: false
      pulloff_mm: 1
      tmc_5160:
        step_pin: i2so.10
        direction_pin: i2so.9:low
        disable_pin: I2SO.8
        cs_pin: NO_PIN
        spi_index: 3
        r_sense_ohms: 0.075
        run_amps: 1.5
        hold_amps: 0.5
        microsteps: 8
        toff_disable: 0
        toff_stealthchop: 5
        use_enable: false
        run_mode: CoolStep
        homing_mode: CoolStep
        stallguard: 3
        stallguard_debug: false
        toff_coolstep: 3
        tpfd: 4
  a:
    steps_per_mm: 157.75
    max_rate_mm_per_min: 18000
    acceleration_mm_per_sec2: 1500
    max_travel_mm: 325
    soft_limits: true
    homing:
      cycle: 1
      positive_direction: true
      mpos_mm: 150
      feed_mm_per_min: 100
      seek_mm_per_min: 800
      settle_ms: 500
      seek_scaler: 1.1
      feed_scaler: 1.1
    motor0:
      limit_neg_pin: NO_PIN
      limit_pos_pin: gpio.32:pu
      limit_all_pin: NO_PIN
      hard_limits: false
      pulloff_mm: 1
      tmc_5160:
        step_pin: i2so.13
        direction_pin: i2so.12
        disable_pin: I2SO.15
        cs_pin: NO_PIN
        spi_index: 4
        r_sense_ohms: 0.022
        run_amps: 0.5
        hold_amps: 0.5
        microsteps: 16
        toff_disable: 0
        toff_stealthchop: 5
        use_enable: false
        run_mode: CoolStep
        homing_mode: CoolStep
        stallguard: 16
        stallguard_debug: false
        toff_coolstep: 3
        tpfd: 4
i2so:
  bck_pin: gpio.22
  data_pin: gpio.21
  ws_pin: gpio.17
spi:
  miso_pin: gpio.19
  mosi_pin: gpio.23
  sck_pin: gpio.18
sdcard:
  cs_pin: gpio.0
  card_detect_pin: NO_PIN
  frequency_hz: 8000000
i2c0:
  sda_pin: gpio.27
  scl_pin: gpio.26
status_outputs:
  report_interval_ms: 500
  idle_pin: I2SO.11:low
  run_pin: I2SO.14:low
  alarm_pin: I2SO.3:low
Laser:
  output_pin: gpio.13:pd
  s0_with_disable: false
  disable_with_s0: false
  speed_map: 0=0.000% 1000=100.000%
  enable_pin: NO_PIN
start:
  must_home: false

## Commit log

2025-07-30 Finish Journal
    [LaserCutter-X GantryBelt Tensioning3.step, LaserCutter-Y Support 1Idler Support.step, LaserCutter.FCStd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]
2025-08-04 finish Journal and submit
    [config.cfg]
